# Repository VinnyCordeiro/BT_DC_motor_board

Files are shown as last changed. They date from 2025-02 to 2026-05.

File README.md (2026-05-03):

# BoxTurtle DC motors standalone board
A standalone board to control the DC motors of the BoxTurtle.

IMPORTANT NOTE: this design is still untested and being modified frequently as bugs/flaws are found. Do not order PCBs yet until we say it's safe!

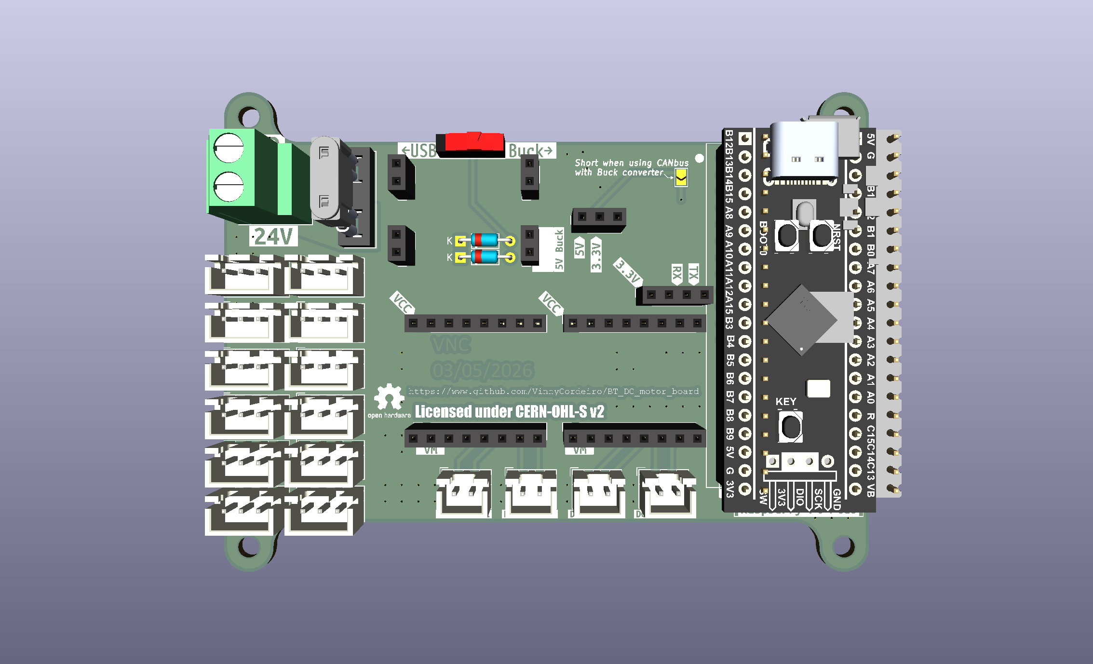
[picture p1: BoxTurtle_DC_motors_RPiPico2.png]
plot


## Why
The [AFC-Lite](https://github.com/xbst/AFC-Lite) is the preferred board for the BoxTurtle, but it is quite expensive and is only available on xbst's store (which is fair). However, many of us (myself included) already have a stash of old 3D printer controller boards to take care of the stepper motors, so only the DC motors were left without a standalone solution to control them. This board is an attempt to solve this situation.

I designed the board to be as easy and cheap as possible; with that in mind, here are the design constraints:
- All components/modules must be through hole mounted: I have professional training in electronics and the tools so SMD isn't a problem, but this isn't true for most of the hobbyists; by using through hole components the soldering complexity barrier is lowered;
- All modules are to be mounted on sockets: this opens some space on the board that would be otherwise unavailable. _DO NOT_ solder the modules directly on the board: not only you'll ruin the modularity of the design, you won't be able to install the power selection circuitry on the board (you may get away by soldering wires at the bottom side of the board for the switch, and solder the diodes at the bottom, but that's a bodge and shouldn't be used);
- I added as much useful information on the board silkscreen as I could, with the exception of the pinout. This should help guiding how the components/modules must be mounted, so it's on you if you let the magic smoke out if mounting them the other way around.

## Bill of Materials
This board was made with modularity in mind, so you'll need to buy those modules from Aliexpress (or any other source as long as the footprint matches; if they don't, you'll need to modify the PCB yourself):
|Component|No. Needed|Comment|Sourcing URL|
|---|---|---|---|
|5.08mm Screw Terminal|1|Power Input|https://www.lcsc.com/product-detail/Screw-span-style-background-color-ff0-terminal-span_MAX-MX129-5-08-02P-GN01-Cu-Y-A_C5188485.html|
|Automotive Mini-Blade Fuse Holder|1|Takes [Mini Automotive Fuses](https://www.keyelco.com/product.cfm/product_id/1376)|https://www.lcsc.com/product-detail/Fuse-Holders_XFCN-XF-506P_C492610.html|
|2A Mini Automotive fuse|1|For circuit safety|https://www.lcsc.com/product-detail/Automotive-Fuses_Littelfuse-0297002-WXNV_C151091.html|
|DC-DC 3A buck converter|1|Pick the 5V version|https://www.aliexpress.com/item/1005007031557776.html|
|LDO 800MA DC 5V to 3.3V buck converter|1|They come with right angle pin headers, you have to swap for straight pins|https://www.aliexpress.com/item/1005007792706354.html|
|DRV8837 2 Way DC H-Bridge|2|Pick the version with 2 drivers on the board|https://www.aliexpress.com/item/1005007587993921.html|
|SN65HVD230 CAN Network Transceiver Board|1|Optional, only if CAN bus will be used. You may need a jumper for the termination resistor if this is at the end of the CAN bus|https://www.aliexpress.com/item/1005006438437964.html|
|Jumper|1|If you doesn't have one|https://www.lcsc.com/product-detail/Shunts-Jumpers_TE-Connectivity-2-881545-2_C5166780.html|
|Pin socket 2 pins|4|For the 5V buck converter module|https://www.lcsc.com/product-detail/Female-Headers_BOOMELE-Boom-Precision-Elec-2-54-1-2P_C49661.html|
|Pin socket 3 pins|1|For the 3.3V buck converter module|https://www.lcsc.com/product-detail/Female-Headers_BOOMELE-Boom-Precision-Elec-2-54-1-3P_C146243.html|
|Pin socket 4 pins|1|For the CAN transceiver module|https://www.lcsc.com/product-detail/Female-Headers_BOOMELE-Boom-Precision-Elec-2-54-1-4P_C2718488.html|
|Pin socket 8 pins|4|For the DRV8837 modules|https://www.lcsc.com/product-detail/Female-Headers_BOOMELE-Boom-Precision-Elec-2-54-1-8P_C27438.html|
|Pin socket 20 pins|2|For the MCU|https://www.lcsc.com/product-detail/Female-Headers_Megastar-ZX-PM2-54-1-20PY_C7499336.html|
|JST XH 2 pins|4|To connect the DC motors|https://www.lcsc.com/product-detail/Wire-To-Board-Connector_JST-B2B-XH-A-LF-SN_C158012.html|
|JST XH 3 pins|12|To connect the endstops|https://www.lcsc.com/product-detail/Wire-To-Board-Connector_JST-B3B-XH-A-LF-SN_C144394.html|
|Schottky diode|2|You can reallistically use whatever through hole Schottky diode you have, even the BAT85 that used to be used on magnetic probes on old VORON releases|https://www.lcsc.com/product-detail/Schottky-Diodes_STMicroelectronics-BAT48_C283476.html|
|Switch|1|For selecting USB ou buck converter power|https://www.lcsc.com/product-detail/Slide-Switches_Korean-Hroparts-Elec-K3-1204D_C145861.html|
|Raspberry Pi Pico, or...|1|MCU (Pick one)|https://www.aliexpress.com/item/1005003708090298.html|
|Raspberry Pi Pico 2, or...|1|MCU (Pick one)|https://pt.aliexpress.com/item/1005005714757487.html|
|STM32F401 BlackPill|1|MCU (Pick one)|https://www.aliexpress.com/item/1005006127461676.html|

## Attributions
- Apex Mk2 Font Family by Jeremy Nelson, licensed under the 1001Fonts Free For Commercial Use License (FFC); obtained at https://www.1001fonts.com/apex-mk2-font.html
- Raspberry Pi Pico STEP file made by Raspberry Pi Foundation; obtained at https://datasheets.raspberrypi.com/pico/Pico-R3-step.zip
- Blackpill STM32F401CCU6 STEP model made by Adam Valent, published on GrabCAD by user Zawisza on August 22nd, 2022; obtained at https://grabcad.com/library/blackpill-stm32f401ccu6-1
- Mini Automotive fuse STEP model by Littelfuse, Inc.; obtained at https://www.littelfuse.com/products/fuses-overcurrent-protection/fuses/automotive-fuses/blade-fuses-shunt/mini/297/0297010-u
- K3-1204D 3D model made by Vinícius N. Cordeiro, using the datasheet as reference. The model isn't completely accurate as it's intended just as a mockup, but the only important feature missing are two 0.5 mm high bumps at the bottom of the switch. The PCB file is already accounting for that.

## Acknowledgements
- [Robert Klotz](https://github.com/ArmoredTurtle) for creating the amazing BoxTurtle project (I'm anxiously awaiting for the 8-Track!);
- [xbst](https://github.com/xbst) for designing the AFC-Lite. While the design files aren't available as I write, the schematics is public so I used them to create this board as well. Also, his mild distaste for the RP2040 MCUs on Klipper projects made me add support for a STM32 MCU board as well, which leads to;
- comradef191 and their [NyoomiesKME board](https://github.com/comradef191/NyoomiesKME) for the idea of adding support for both the Raspberry Pi Pico and the Black Pill STM32F401 MCU modules;
- Sanity Agathion on the [VORON Discord server](https://discord.gg/voron) for the tip that made me add the CAN bus module support;
- [timmit99](https://github.com/timmit99/) and [Shammy](https://xrbunker.works), both also from the VORON Discord server, for the support and also for providing a 3D model for the fuse holder (just catch the ball next time, Tim!);
- and [clee](https://github.com/clee): you know what you did.

## LICENSE
Copyright Vinícius N. Cordeiro 2025-2026

This source describes Open Hardware and is licensed under the CERN-OHL-S v2 or any later version.
You may redistribute and modify this source and make products using it under the terms of the CERN-OHL-S v2. (https://ohwr.org/cern_ohl_s_v2.txt)

This source is distributed WITHOUT ANY EXPRESS OR IMPLIED WARRANTY, INCLUDING OF MERCHANTABILITY, SATISFACTORY QUALITY AND FITNESS FOR A PARTICULAR PURPOSE. Please see the CERN-OHL-S v2 for applicable conditions.

Source Location: https://github.com/VinnyCordeiro/BT_DC_motor_board

As per CERN-OHL-S v2 section 4, should You produce hardware based on this source, You must where practicable maintain the Source Location visible on the PCB.

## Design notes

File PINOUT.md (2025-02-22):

# Pinout:

## Endstops

|Endstop|RPi Pico*|Black Pill|
|---|---|---|
|1|gpio22|PA5|
|2|gpio20|PA3|
|3|gpio18|PA1|
|4|gpio16|PC15|
|5|gpio13|PB9|
|6|gpio15|PB1|
|7|gpio26|PA6|
|8|gpio21|PA4|
|9|gpio19|PA2|
|10|gpio17|PA0|
|11|gpio12|PB8|
|12|gpio14|PC14|

## CAN bus

|Function|RPi Pico*|Black Pill|
|---|---|---|
|CAN-TX|gpio27|PA7|
|CAN-RX|gpio28|PB0|

## DC motors

### Motor 1

|Function|RPi Pico*|Black Pill|
|---|---|---|
|SLP_1|gpio0|PB12|
|DC1_1|gpio1|PB13|
|DC2_1|gpio2|PB15|

### Motor 2

|Function|RPi Pico*|Black Pill|
|---|---|---|
|SLP_2|gpio3|PA8|
|DC1_2|gpio4|PA9|
|DC2_2|gpio5|PA10|

### Motor 3

|Function|RPi Pico*|Black Pill|
|---|---|---|
|SLP_3|gpio11|PB7|
|DC1_3|gpio10|PB6|
|DC2_3|gpio9|PB5|

### Motor 4

|Function|RPi Pico*|Black Pill|
|---|---|---|
|SLP_4|gpio8|PB4|
|DC1_4|gpio7|PB3|
|DC2_4|gpio6|PA15|

\* While this board was designed using the original Raspberry Pi Pico, it _should_ work with the Raspberry Pi Pico 2, which uses the RP2350A MCU.

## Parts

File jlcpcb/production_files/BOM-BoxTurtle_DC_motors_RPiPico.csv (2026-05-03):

Comment | Designator | Footprint | LCSC | Quantity
AMS1117 module | J5 | PinSocket_1x03_P2.54mm_Vertical | C146243 | 1
BAT85 | D1,D2 | D_DO-35_SOD27_P7.62mm_Horizontal | C3312828 | 2
CAN | J15 | PinSocket_1x04_P2.54mm_Vertical | C2718488 | 1
Conn_01x03 | SW1,SW10,SW11,SW12,SW2,SW3,SW4,SW5,SW6,SW7,SW8,SW9 | JST_XH_B3B-XH-A_1x03_P2.50mm_Vertical | C144394 | 12
DC motor 1 | J10 | JST_XH_B2B-XH-A_1x02_P2.50mm_Vertical | C158012 | 1
DC motor 2 | J11 | JST_XH_B2B-XH-A_1x02_P2.50mm_Vertical | C158012 | 1
DC motor 3 | J12 | JST_XH_B2B-XH-A_1x02_P2.50mm_Vertical | C158012 | 1
DC motor 4 | J13 | JST_XH_B2B-XH-A_1x02_P2.50mm_Vertical | C158012 | 1
DRV8837 module left | J6,J8 | PinSocket_1x08_P2.54mm_Vertical | C27438 | 2
DRV8837 module right | J7,J9 | PinSocket_1x08_P2.54mm_Vertical | C27438 | 2
Fuse_Small | F1 | XF-506P | C492610 | 1
K3-1204D | SW13 | K3-1204D | C145861 | 1
Power input | J1,J2 | PinSocket_1x02_P2.54mm_Vertical | C49661 | 2
Power output | J3,J4 | PinSocket_1x02_P2.54mm_Vertical | C49661 | 2
Screw_Terminal_01x02 | J14 | TerminalBlock_Phoenix_MKDS-3-2-5.08_1x02_P5.08mm_Horizontal | C5188485 | 1
Raspberry Pi Pico | U1 | Pico |  | 1
Black Pill STM32F401 | U2 | STM32F401 Black Pill |  | 1
Jumper_2_Small_Open | JP2 | SolderJumper-2_P1.3mm_Open_TrianglePad1.0x1.5mm |  | 1

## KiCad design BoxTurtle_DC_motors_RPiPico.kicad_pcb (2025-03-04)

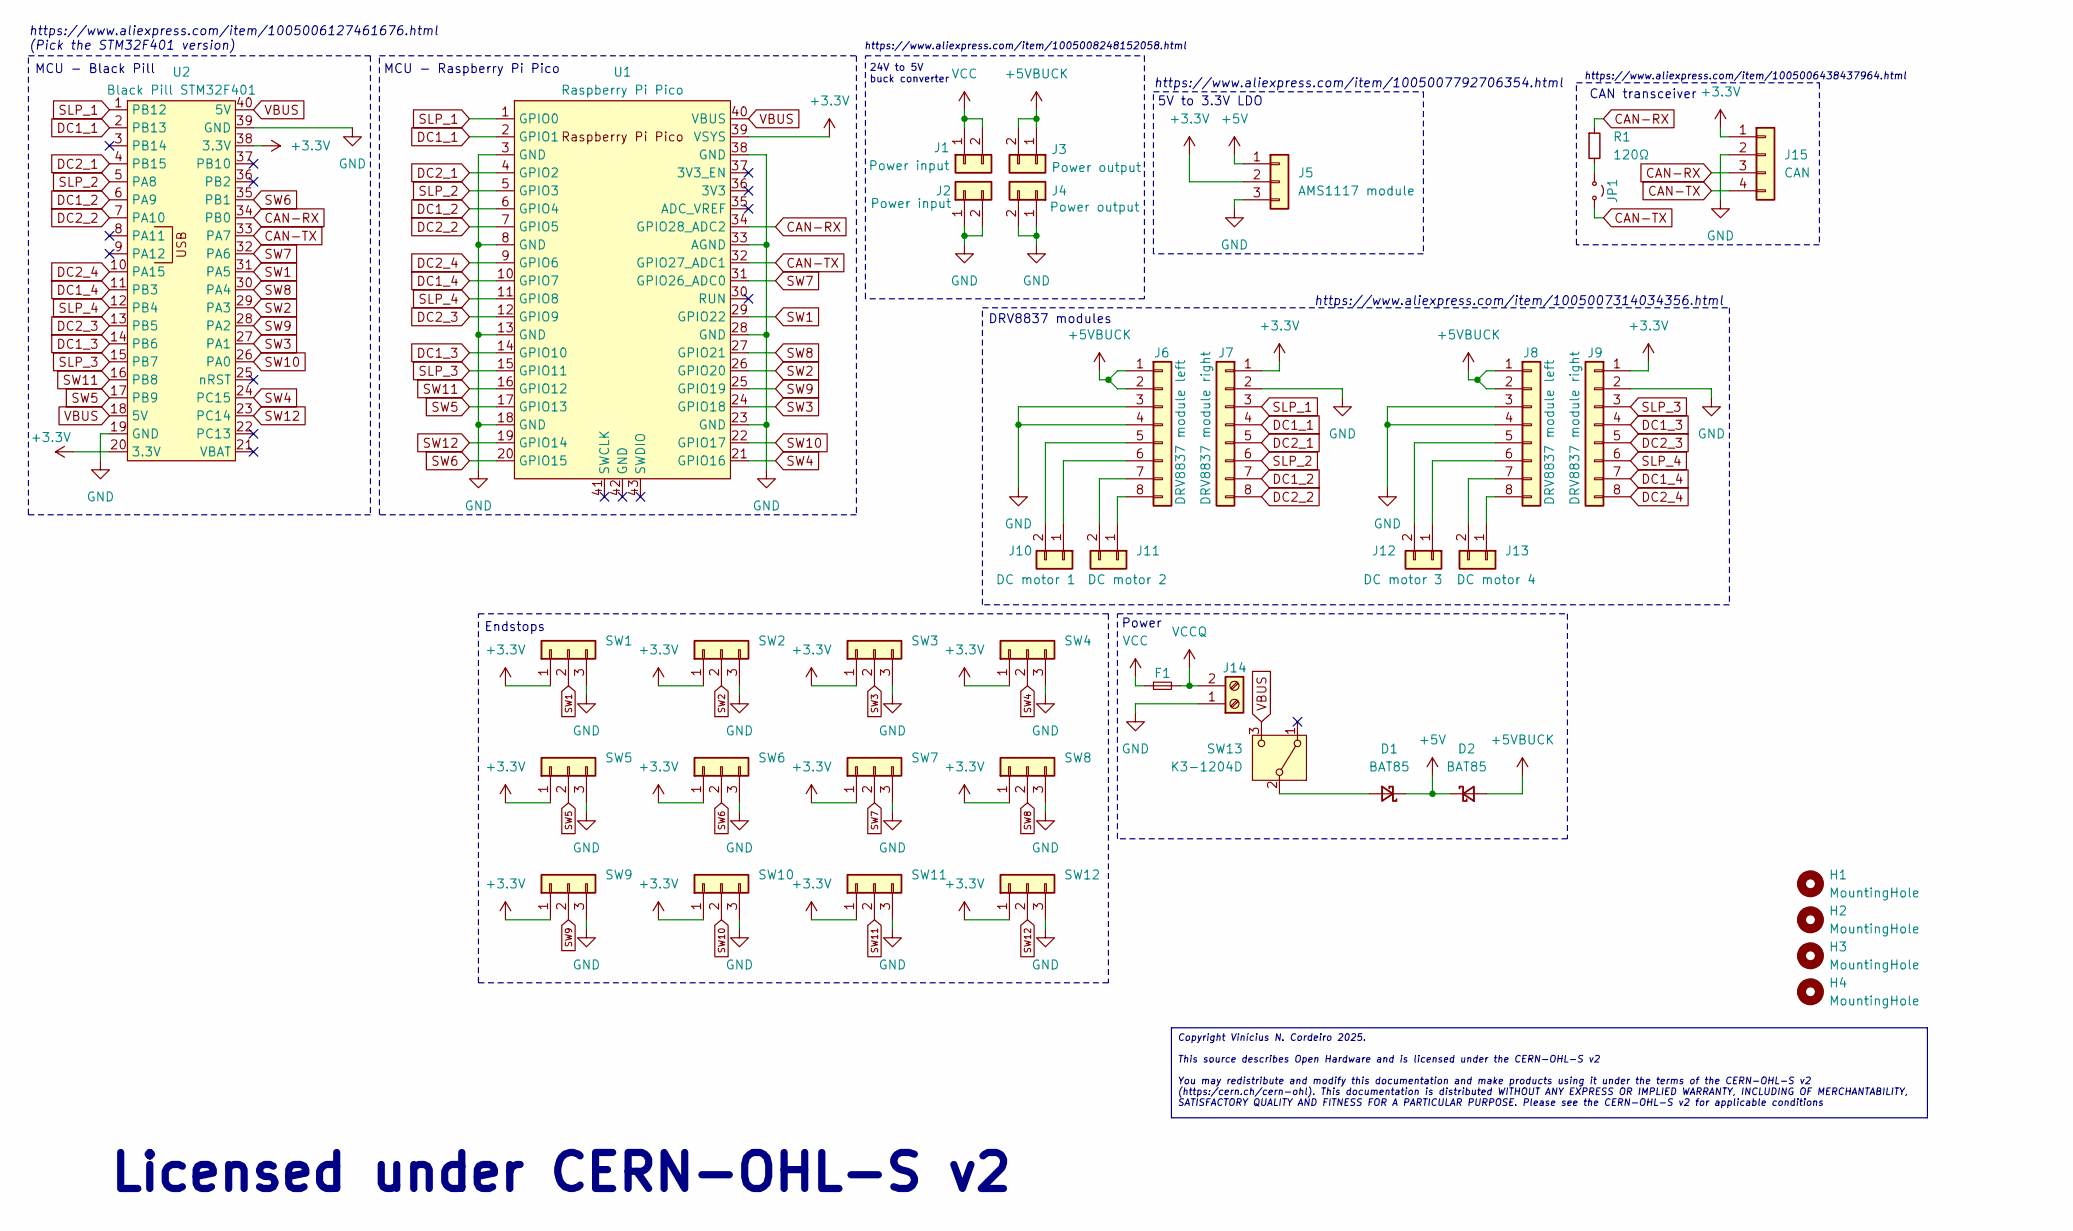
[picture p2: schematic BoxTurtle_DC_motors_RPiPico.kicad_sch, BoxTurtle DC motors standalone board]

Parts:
D1, D2: BAT85; D_DO-35_SOD27_P7.62mm_Horizontal
F1: Fuse_Small; XF-506P
H1, H2, H3, H4: MountingHole; MountingHole_3.2mm_M3
J1, J2: Power input; PinSocket_1x02_P2.54mm_Vertical
J3, J4: Power output; PinSocket_1x02_P2.54mm_Vertical
J5: AMS1117 module; PinSocket_1x03_P2.54mm_Vertical
J6, J8: DRV8837 module left; PinSocket_1x08_P2.54mm_Vertical
J7, J9: DRV8837 module right; PinSocket_1x08_P2.54mm_Vertical
J10: DC motor 1; JST_XH_B2B-XH-A_1x02_P2.50mm_Vertical
J11: DC motor 2; JST_XH_B2B-XH-A_1x02_P2.50mm_Vertical
J12: DC motor 3; JST_XH_B2B-XH-A_1x02_P2.50mm_Vertical
J13: DC motor 4; JST_XH_B2B-XH-A_1x02_P2.50mm_Vertical
J14: Screw_Terminal_01x02; TerminalBlock_Phoenix_MKDS-3-2-5.08_1x02_P5.08mm_Horizontal
J15: CAN; PinSocket_1x04_P2.54mm_Vertical
JP1: Jumper_2_Small_Open; PinHeader_1x02_P2.54mm_Vertical
R1: 120Ω; R_Axial_DIN0207_L6.3mm_D2.5mm_P10.16mm_Horizontal
SW1, SW2, SW3, SW4, SW5, SW6, SW7, SW8, SW9, SW10, SW11, SW12: Conn_01x03; JST_XH_B3B-XH-A_1x03_P2.50mm_Vertical
SW13: K3-1204D; LCSC C273395
U1: Raspberry Pi Pico; Pico
U2: Black Pill STM32F401; STM32F401 Black Pill

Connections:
+3.3V: J5.2, J7.1, J9.1, J15.1, SW1.1, SW2.1, SW3.1, SW4.1, SW5.1, SW6.1, SW7.1, SW8.1, SW9.1, SW10.1, SW11.1, SW12.1, U1.39 (VSYS), U2.20 (3.3V), U2.38 (3.3V)
+5V: D1.1 (K), D2.1 (K), J5.1
+5VBUCK: D2.2 (A), J3.1, J3.2, J6.1, J6.2, J8.1, J8.2
CAN-RX: J15.3, R1.1, U1.34 (GPIO28_ADC2), U2.34 (PB0)
CAN-TX: J15.4, JP1.2 (B), U1.32 (GPIO27_ADC1), U2.33 (PA7)
DC1_1: J7.4, U1.2 (GPIO1), U2.2 (PB13)
DC1_2: J7.7, U1.6 (GPIO4), U2.6 (PA9)
DC1_3: J9.4, U1.14 (GPIO10), U2.14 (PB6)
DC1_4: J9.7, U1.10 (GPIO7), U2.11 (PB3)
DC2_1: J7.5, U1.4 (GPIO2), U2.4 (PB15)
DC2_2: J7.8, U1.7 (GPIO5), U2.7 (PA10)
DC2_3: J9.5, U1.12 (GPIO9), U2.13 (PB5)
DC2_4: J9.8, U1.9 (GPIO6), U2.10 (PA15)
GND: J2.1, J2.2, J4.1, J4.2, J5.3, J6.3, J6.4, J7.2, J8.3, J8.4, J9.2, J14.1, J15.2, SW1.3, SW2.3, SW3.3, SW4.3, SW5.3, SW6.3, SW7.3, SW8.3, SW9.3, SW10.3, SW11.3, SW12.3, U1.3 (GND), U1.8 (GND), U1.13 (GND), U1.18 (GND), U1.23 (GND), U1.28 (GND), U1.33 (AGND), U1.38 (GND), U2.19 (GND), U2.39 (GND)
unnamed: D1.2 (A), SW13.2 (B)
unnamed: J6.6, J10.1
unnamed: J6.5, J10.2
unnamed: J6.8, J11.1
unnamed: J6.7, J11.2
unnamed: J8.6, J12.1
unnamed: J8.5, J12.2
unnamed: J8.8, J13.1
unnamed: J8.7, J13.2
unnamed: JP1.1 (A), R1.2
SLP_1: J7.3, U1.1 (GPIO0), U2.1 (PB12)
SLP_2: J7.6, U1.5 (GPIO3), U2.5 (PA8)
SLP_3: J9.3, U1.15 (GPIO11), U2.15 (PB7)
SLP_4: J9.6, U1.11 (GPIO8), U2.12 (PB4)
SW1: SW1.2, U1.29 (GPIO22), U2.31 (PA5)
SW2: SW2.2, U1.26 (GPIO20), U2.29 (PA3)
SW3: SW3.2, U1.24 (GPIO18), U2.27 (PA1)
SW4: SW4.2, U1.21 (GPIO16), U2.24 (PC15)
SW5: SW5.2, U1.17 (GPIO13), U2.17 (PB9)
SW6: SW6.2, U1.20 (GPIO15), U2.35 (PB1)
SW7: SW7.2, U1.31 (GPIO26_ADC0), U2.32 (PA6)
SW8: SW8.2, U1.27 (GPIO21), U2.30 (PA4)
SW9: SW9.2, U1.25 (GPIO19), U2.28 (PA2)
SW10: SW10.2, U1.22 (GPIO17), U2.26 (PA0)
SW11: SW11.2, U1.16 (GPIO12), U2.16 (PB8)
SW12: SW12.2, U1.19 (GPIO14), U2.23 (PC14)
VBUS: SW13.3 (C), U1.40 (VBUS), U2.18 (5V), U2.40 (5V)
VCC: F1.1, J1.1, J1.2
VCCQ: F1.2, J14.2

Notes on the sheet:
Copyright Vinícius N. Cordeiro 2025. This source describes Open Hardware and is licensed under the CERN-OHL-S v2 You may redistribute and modify this documentation and make products using it under the terms of the CERN-OHL-S v2 (https:/cern.ch/cern-ohl). This documentation is distributed WITHOUT AN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
CAN transceiver
MCU - Raspberry Pi Pico
https://www.aliexpress.com/item/1005006127461676.html (Pick the STM32F401 version)
Licensed under CERN-OHL-S v2
https://www.aliexpress.com/item/1005006438437964.html
5V to 3.3V LDO
https://www.aliexpress.com/item/1005007792706354.html
MCU - Black Pill
https://www.aliexpress.com/item/1005008248152058.html
Endstops
24V to 5V buck converter
DRV8837 modules
https://www.aliexpress.com/item/1005007314034356.html
Power

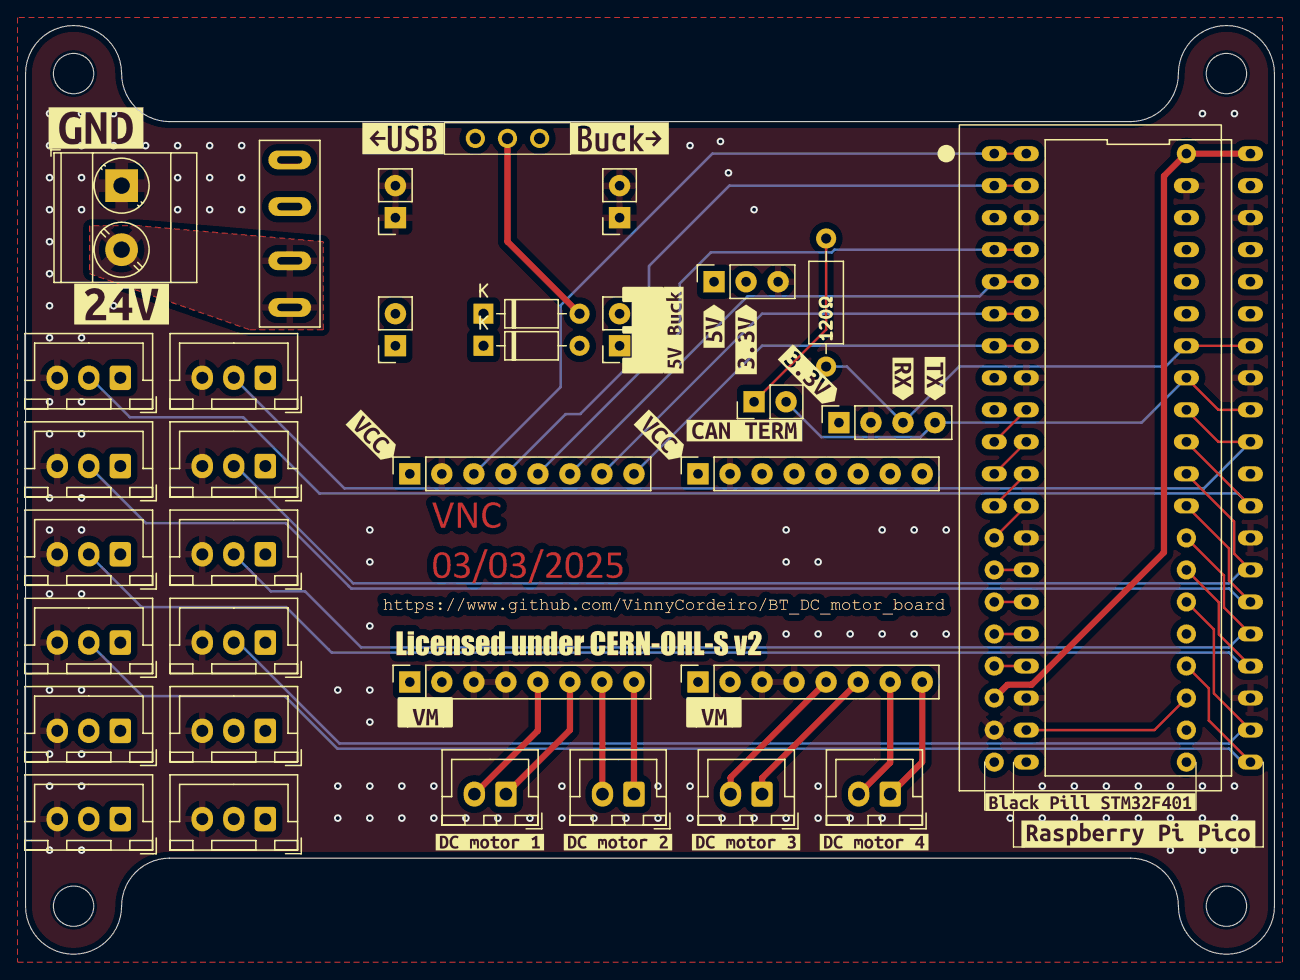
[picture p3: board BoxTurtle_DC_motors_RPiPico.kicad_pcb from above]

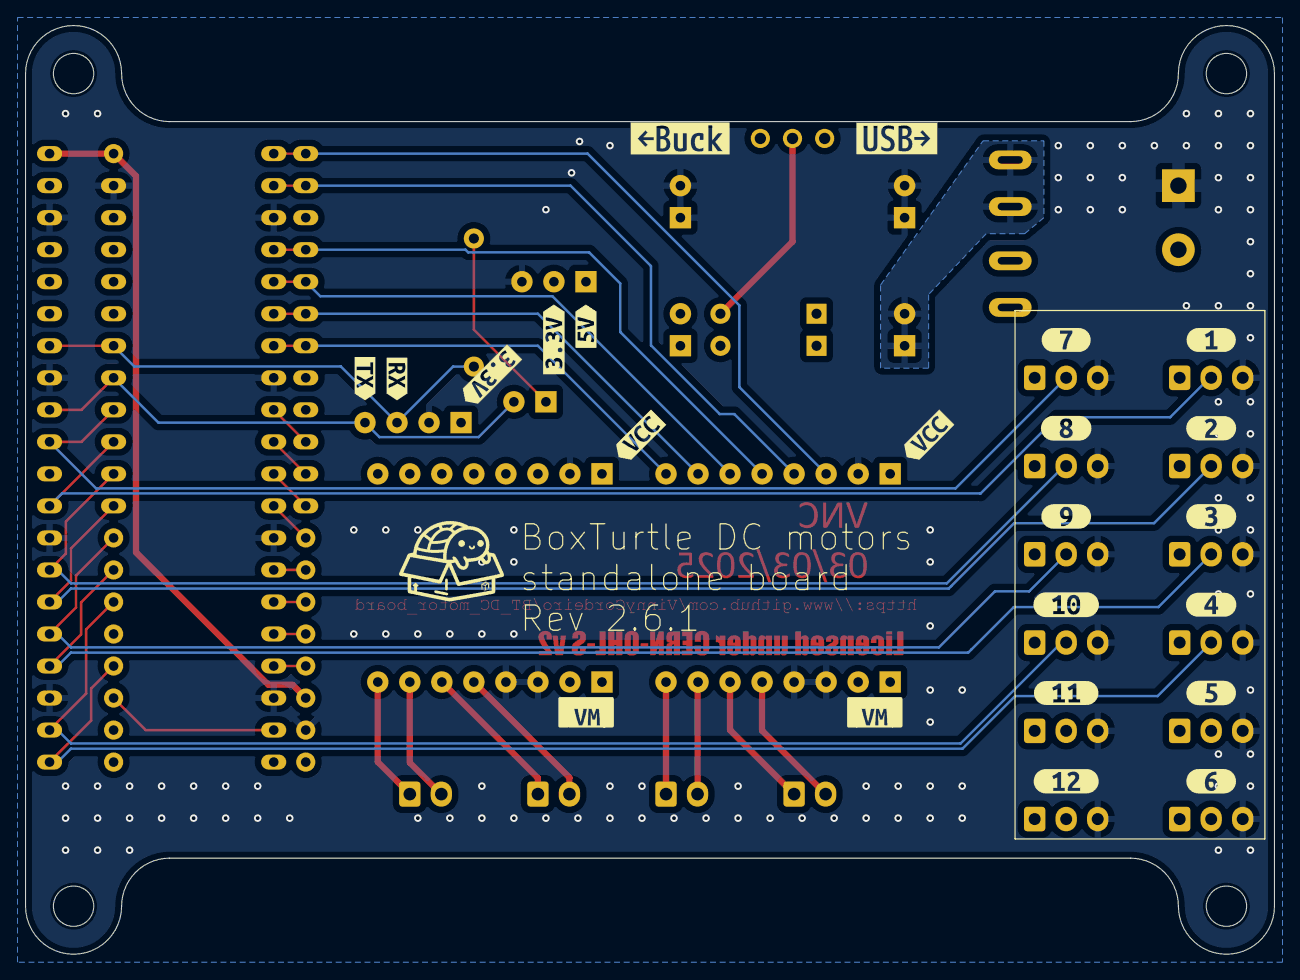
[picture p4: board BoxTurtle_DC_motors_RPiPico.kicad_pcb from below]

Board: 4 copper layers, 99.1 x 73.7 mm, 83 parts (23 on the bottom side), 43 nets.

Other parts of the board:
kibuzzard-67A0CA07: G***; kibuzzard-67A0CA07
kibuzzard-67A0043B: G***; kibuzzard-67A0043B
kibuzzard-67A00413: G***; kibuzzard-67A00413
kibuzzard-67C5FAD7: G***; kibuzzard-67C5FAD7
kibuzzard-67C5FB16: G***; kibuzzard-67C5FB16
kibuzzard-67C5FB88: G***; kibuzzard-67C5FB88
kibuzzard-67C5FBBE: G***; kibuzzard-67C5FBBE
kibuzzard-67C627D9: G***; kibuzzard-67C627D9
kibuzzard-67C627E2: G***; kibuzzard-67C627E2
kibuzzard-67C627EC: G***; kibuzzard-67C627EC
kibuzzard-67C627F5: G***; kibuzzard-67C627F5
kibuzzard-67C628B6: G***; kibuzzard-67C628B6
kibuzzard-67C628BD: G***; kibuzzard-67C628BD
kibuzzard-67C6285C: G***; kibuzzard-67C6285C
kibuzzard-67C6289C: G***; kibuzzard-67C6289C
kibuzzard-679EE0D3: G***; kibuzzard-679EE0D3
kibuzzard-679EE0F2: G***; kibuzzard-679EE0F2
kibuzzard-679EE1A8: G***; kibuzzard-679EE1A8
kibuzzard-679EE1B2: G***; kibuzzard-679EE1B2
kibuzzard-679EE6D0: G***; kibuzzard-679EE6D0
kibuzzard-679EE6DA: G***; kibuzzard-679EE6DA
kibuzzard-679EE6E6: G***; kibuzzard-679EE6E6
kibuzzard-679EE19C: G***; kibuzzard-679EE19C
kibuzzard-679EE64B: G***; kibuzzard-679EE64B
kibuzzard-679EE68A: G***; kibuzzard-679EE68A
kibuzzard-679EE72D: G***; kibuzzard-679EE72D
kibuzzard-679EE78C: G***; kibuzzard-679EE78C
kibuzzard-679EE189: G***; kibuzzard-679EE189
kibuzzard-679EE681: G***; kibuzzard-679EE681
kibuzzard-679EE693: G***; kibuzzard-679EE693
kibuzzard-679EE762: G***; kibuzzard-679EE762
kibuzzard-679EE772: G***; kibuzzard-679EE772
kibuzzard-679EE781: G***; kibuzzard-679EE781
kibuzzard-679EE822, kibuzzard-679EE822#2, kibuzzard-679EE822#3, kibuzzard-679EE822#4: G***; kibuzzard-679EE822
kibuzzard-679EE836, kibuzzard-679EE836#2: G***; kibuzzard-679EE836
kibuzzard-679FA142, kibuzzard-679FA142#2: G***; kibuzzard-679FA142
kibuzzard-679FA150, kibuzzard-679FA150#2: G***; kibuzzard-679FA150
kibuzzard-679FB212: G***; kibuzzard-679FB212

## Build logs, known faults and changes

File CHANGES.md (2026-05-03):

- 2025-02-01:
  - Revision 1.0: board only using Raspberry Pi Pico as the MCU
- 2025-02-02:
  - Revision 1.1:
    - added CAN bus support by adding a connector for a CAN transceiver module and additional support circuitry
  - Revision 2.0:
    - added support for the Black Pill STM32F401 MCU
    - added circuitry to select between USB power and buck converter power
- 2025-02-03:
  - Revision 2.1:
    - first publicly available revision
    - made some corrections on silkscreen
    - added the necessary CERN Licence information
  - Revision 2.2:
    - added a fuse
    - created file documenting the pinout
  - Revision 2.3:
    - corrected a flaw that could blow a USB port when the board tries to power the DC motors from USB
    - formatted CHANGES.md a little better
    - added a note informing that the design is still untested
- 2025-02-04:
  - added a tentative config file
- 2025-02-05:
  - corrected info about the fuse
  - added fuse 3D model
- 2025-02-22:
  - Revision 2.4:
    - bigger footprint for the CAN terminator resistor
    - the diameter of the holes for the sockets that hold the Raspberry Pi Pico now matches the ones for the Black Pill for a snugger fit, that helps when soldering
    - SW6 changed pin on the Black Pill, now being PB1; the previous pin is shared with the on-board LED and that could lead to strange behavior
- 2025-02-25:
  - Revision 2.5:
    - corrected the footprint for both the 24V to 5V and the DRV8837 modules
    - added a source for a Raspberry Pi Pico 2 clone on the BOM
    - uploaded Rev. 2.5 Gerber files
- 2025-03-03:
  - Revision 2.6:
    - corrected the footprint for the 24V to 5V buck converter module again: Aliexpress finally delivered it and I could use it on a printed mock-up to get the real dimensions (as originally I was only guessing it using photos as a reference. It was pretty close, but innacurate enough so I had to change it)
    - changed the switch for 5V source selection for a model that has both a smaller footprint and a bigger current capacity
    - changed all hole diameters for pin sockets
  - Revision 2.6.1:
    - adjusted some silkscreen markings
    - uploaded updated Gerber files
- 2025-03-04:
  - Added the JST XH connectors to the BOM
- 2026-04-26
  - Revision 2.6.2:
    - adjusted the footprint for the 24V to 5V buck converter module yet again
    - changed the endstops to follow the same pinout as the AFC Lite
    - uploaded updated Gerber files
    - corrected typo on README.md
- 2026-05-02
  - Revision 2.6.3:
    - added a solder jumper to allow usage of the board with CAN bus while powered by the 24V to 5V buck converter module (terrible oversight that only now was caught)
    - updated some of the silkscreen
    - uploaded updated Gerber files
- 2026-05-03
  - Revision 2.6.4:
    - removed the 120 ohms resistor and the headers for it as they aren't needed, the CAN bus transceiver module already includes a resistor and the headers for a jumper to activate it
    - turned the DC motors connectors 180 degrees, so it doesn't trigger my OCD anymore and are aligned with the endstop connectors
    - updated some of the silkscreen, including OSHW and KiCad logos
    - made some clarifications on older entries of CHANGES.md

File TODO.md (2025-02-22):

2025-02-03:
- Add a fuse on the power input: DONE!
- Write the pinout documentation: DONE!
- Write an example config file: DONE!

2025-02-22:
- Change terminal block for Molex Microfit 3.0 connector (still in study)

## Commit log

2025-02-03 Initial release
    [BoxTurtle_DC_motors_RPiPico.kicad_pcb, BoxTurtle_DC_motors_RPiPico.kicad_sch]
2025-02-03 Fuse & Gerber
    Added the fuse for safety, also uploaded Gerber files for those who want to make their own board.
    [BOM-BoxTurtle_DC_motors_RPiPico.csv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]
2025-02-03 Added fuse holder 3D model part 1
    Changes for the PCB file and README.md; also included a render of the board that will be inserted on the README.md later.
    [BoxTurtle_DC_motors_RPiPico.kicad_pcb]
2025-02-03 Added fuse holder 3D model part 2
    The fuse holder 3D model itself.
2025-02-03 Update README.md
    Added the inner marking to display the board's render.
2025-02-03 Corrected 5V source for DC motors
    As it was this board will blow your USB port.
    [BoxTurtle_DC_motors_RPiPico.kicad_pcb, BoxTurtle_DC_motors_RPiPico.kicad_sch]
2025-02-03 Correct fatal flaw on 5V supply for DC motors
    [BOM-BoxTurtle_DC_motors_RPiPico.csv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]
2025-02-04 Initial release of config file
    This should be added at the config/mcu directory of the AFC Klipper add-on. Subject to testing.
    [BT_DC_PCB.cfg]
2025-02-05 Update README.md
    Corrected info about the fuse
2025-02-05 Update CHANGES.md
    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
2025-02-05 Updated PCB
    Modified some more silkscreens, added a fuse 3D model
    [BoxTurtle_DC_motors_RPiPico.kicad_pcb]
2025-02-05 Fuse 3D model
    Downloaded from Littelfuse website
2025-02-22 Update PINOUT.md
    Changed SW6 from PC13 to PB1 on the Black Pill because that pin is shared with the LED and that could lead to strange behavior.
2025-02-22 Revision 2.4 - QoL updates
    Increased CAN bus resistor footprint; reduced hole diameter on Raspberry Pi Pico's socket pads for snugger fit; changed pin for SW6 on the Black Pill.
    [BoxTurtle_DC_motors_RPiPico.kicad_pcb, BoxTurtle_DC_motors_RPiPico.kicad_sch]
2025-02-22 Update BT_DC_PCB.cfg
    SW6 on the Black Pill is now on PB1
    [BT_DC_PCB.cfg]
2025-02-22 Update README.md
    Changed fuse to 5A, the previous one was excessively high current.
2025-02-25 Revision 2.5
    Corrected the footprint for the 24V to 5V buck converter and the DRV8837 modules.
    [BoxTurtle_DC_motors_RPiPico.kicad_pcb]
2025-02-26 Update README.md
    Added a source for the Raspberry Pi Pico 2 (actually a clone using USB Type C receptacle because we are in 2025), corrected a typo.
2025-02-26 Rev. 2.5 Gerber files
    Forgot to upload earlier...
    [BOM-BoxTurtle_DC_motors_RPiPico.csv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]
2025-03-03 Update README.md
    Changed the fuse again, changed the switch as the old one is too big for the footprint changes that are needed.
2025-03-03 Revision 2.6
    Updated footprints again now that I have them on hand to accurately make measures, changed selection switch for a model that is smaller and carry more current.
    [BoxTurtle_DC_motors_RPiPico.kicad_pcb, BoxTurtle_DC_motors_RPiPico.kicad_sch]
2025-03-03 Revision 2.6 Gerber files
    [BOM-BoxTurtle_DC_motors_RPiPico.csv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]
2025-03-04 Revision 2.6.1
    Just silkscreen changes
    [BoxTurtle_DC_motors_RPiPico.kicad_pcb]
2025-03-04 Revision 2.6.1
    Minor silkscreen markings adjustments.
    [BoxTurtle_DC_motors_RPiPico-CuBottom.gbr, BoxTurtle_DC_motors_RPiPico-CuIn1.gbr, BoxTurtle_DC_motors_RPiPico-CuIn2.gbr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]
2025-03-04 Update README.md
    Added the JST XH connectors
2026-04-26 Revision 2.6.2
    1. adjusted sockets for buck converter; 2. adjusted endstops to follow same pattern as AFC Lite
    [BoxTurtle_DC_motors_RPiPico.kicad_sch]
2026-04-26 Revision 2.6.2 - DRC errors correction
    Had to correct them to generate the Gerber files.
2026-04-26 Revision 2.6.2 - Gerber & production files
    [BOM-BoxTurtle_DC_motors_RPiPico.csv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]
2026-05-02 Revision 2.6.3
    Added a solder jumper for powering the microcontroller board while using CANbus; updated silkscreen.
    [BoxTurtle_DC_motors_RPiPico.kicad_sch]
2026-05-02 Revision 2.6.3 - Gerber & production files
    [BOM-BoxTurtle_DC_motors_RPiPico.csv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]
2026-05-03 Update README.md
    Excluded the line in the BOM with the 120 ohms resistor, it's already included on the CAN transceiver board.
2026-05-03 Revision 2.6.4
    Will update the Gerber files later
    [BoxTurtle_DC_motors_RPiPico.kicad_sch]
2026-05-03 Revision 2.6.4 - Gerber & production files
    [BOM-BoxTurtle_DC_motors_RPiPico.csv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]
2026-05-03 Update README.md
    Forgot to delete a line in the BOM: the pin header for the 120 ohms resistor that now isn't there anymore.
2026-05-03 Update README.md
    Dead link for the Raspberry Pi Pico 2 corrected
